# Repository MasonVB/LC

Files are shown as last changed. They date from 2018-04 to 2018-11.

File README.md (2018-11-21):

## DESIGN AND CONTROL OF A HIGH PRECISION LASER CUTTING MACHINE
  This repository includes all files files related to the reproduction of a high precision laser cutting machine. This machine is the topic of paper IMECE2018-88131 from the ASME 2018 International Mechanical Engineering Congress and Exposition, November 9-15, 2018, Pittsburgh, Pennsylvania, USA

  This repository is divided into three sections: the SolidWorks model, the .STL files used by 3D printers, and the drawings for each of the parts. 

  * To open the SolidWorks model: download the repository, navigate to the 3D Model Files - Solidworks folder, and open the LCOA-1.SLDASM file. For reference, all part numbers are described in the PN file located in the root folder.

  * To open the .STL files: download the repository and navigate to the 3D Printer Files folder.

  * To open the drawing files: download the repository, navigate to the Drawing Files folder, and then to the PDF folder. PDF versions of each drawing is located here.
  
### Please note:
This is an ongoing project. Therefore, although the 3D Printing files (.STL) should be up to date, the most up to date files will be the SolidWorks models. 

  Additionally, although there are drawing files for every part, only pertinent dimensions are given. As stated on every drawing, all dimensions are for reference and part fabrication shall be performed according to the solid models. If any discrepancies occur, the solid model shall be assumed to be correct.

  For more information or any questions, please contact me through the form located at the bottom of my website: www.MasonVB.com.

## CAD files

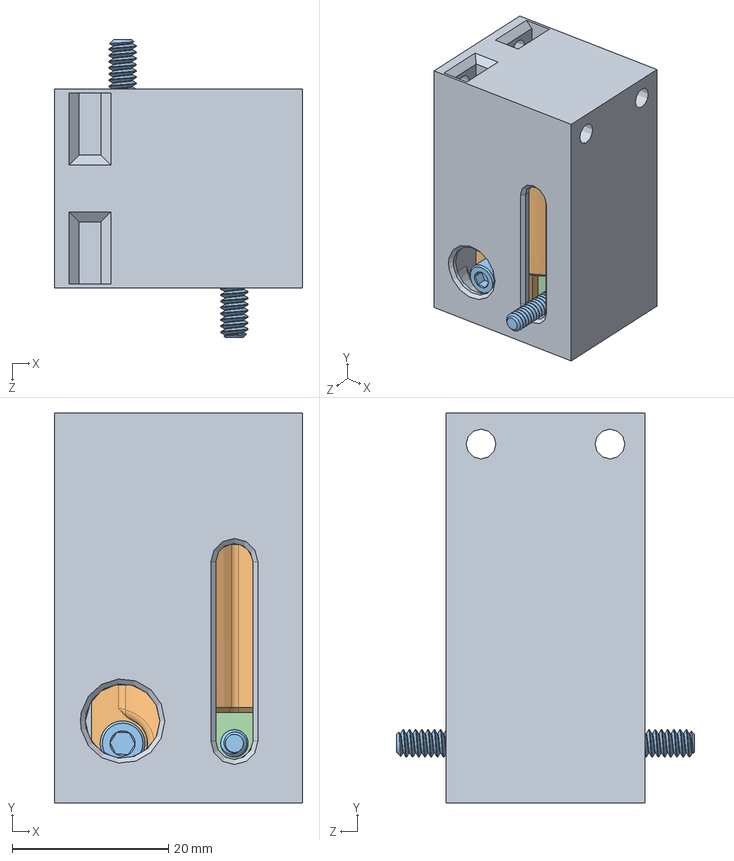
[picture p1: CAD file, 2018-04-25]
Pen Adapter/PEN ADAPTER.SLDASM
31.8 x 49.8 x 38.1 mm
PEN SLEEVE
PEN ADAPTER
92196A153 x 2
94855A201 x 2

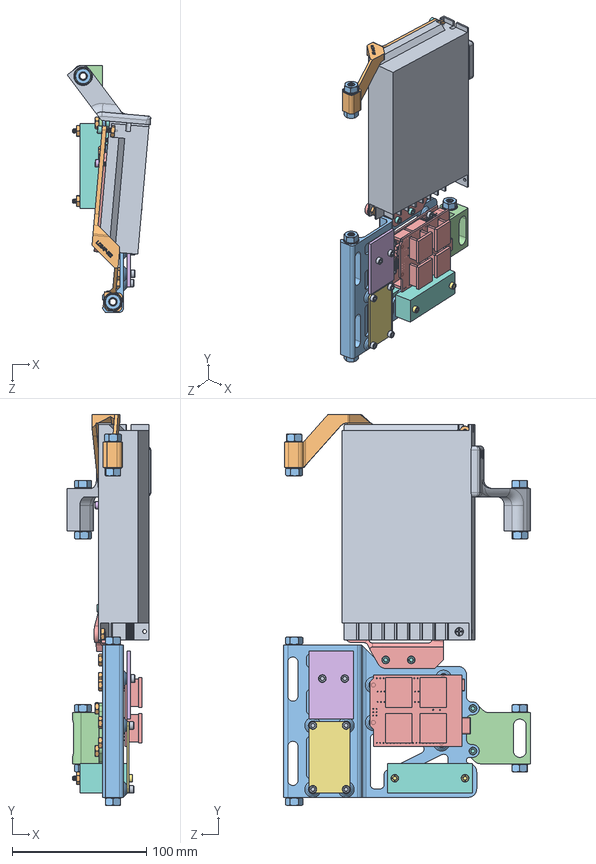
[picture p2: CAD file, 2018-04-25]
3D Model Files - Solidworks/LCSA-5.SLDASM
62.4 x 291.7 x 184.2 mm
LCSAP-501
LCSAP-502
LCSAP-503
LCSAP-504
LCSAP-505
91292A111 x 3
92196A237 x 2
92196A145 x 6
97334A146 x 10
90480A007 x 19
90473A029 x 8
91090A105 x 8
UNO-CNC
3.3V-5V
TB-1505L x 2
LRS-150-12
92210A145

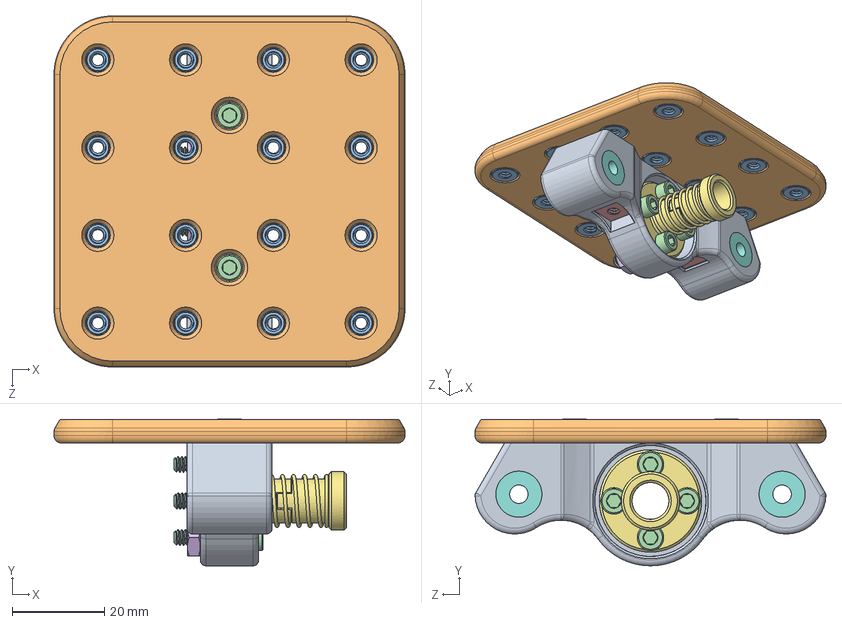
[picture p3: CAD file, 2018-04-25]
3D Model Files - Solidworks/LCSA-2.SLDASM
76.2 x 31.9 x 76.2 mm
LCSAP-202
LCSAP-201
95117A433 x 16
92196A150 x 6
94855A201 x 2
90480A007 x 4
T8-AB
6659K650 x 2

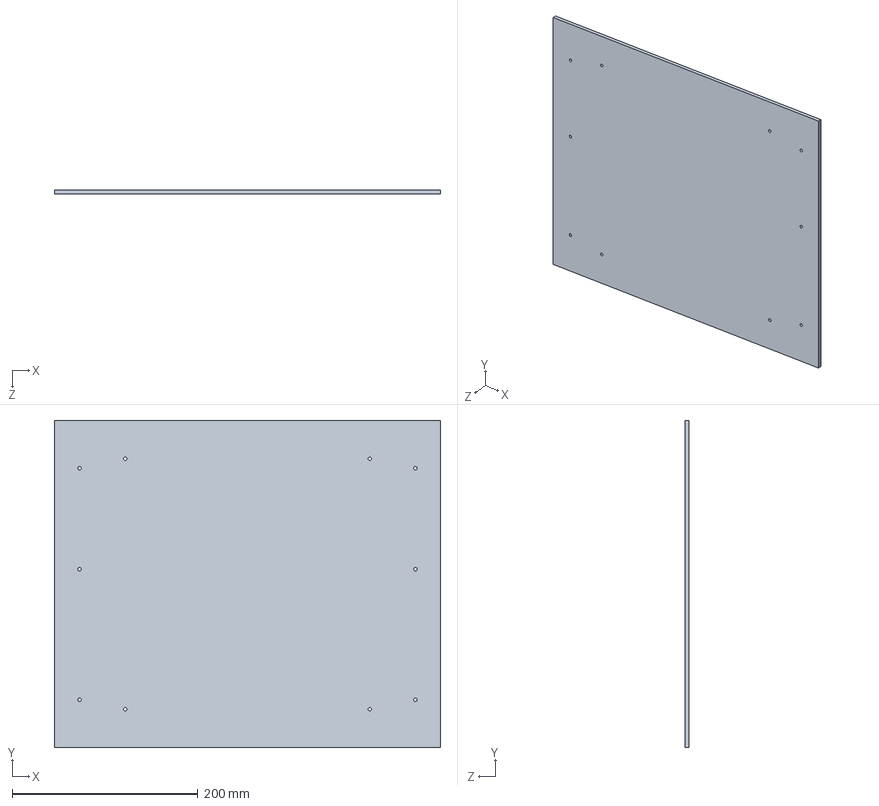
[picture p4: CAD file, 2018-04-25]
3D Model Files - Solidworks/LCSAP-607.SLDPRT
415.9 x 352.4 x 4.76 mm

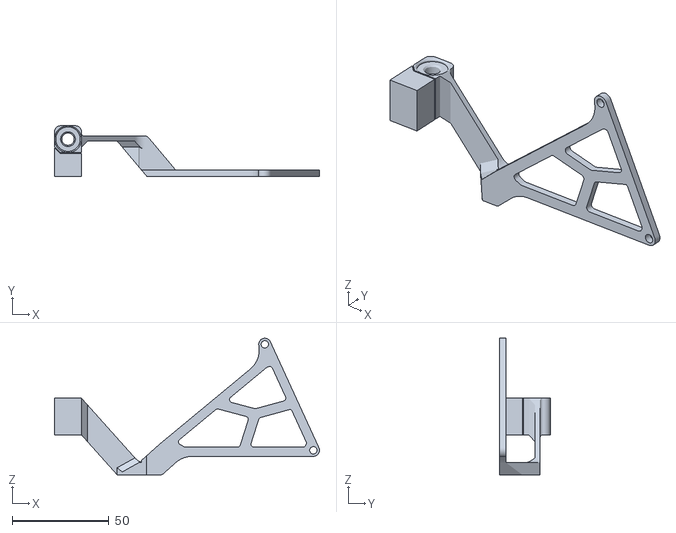
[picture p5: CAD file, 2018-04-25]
3D Printer Files/LCSAP-502.STL
137.2 x 26.2 x 70.7

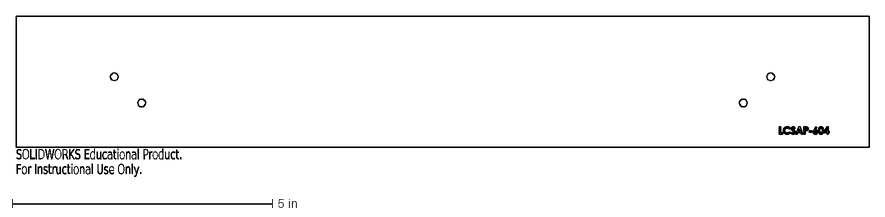
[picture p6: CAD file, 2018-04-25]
Laser Files/LCSAP-604.DXF
SOLIDWORKS Educational Product.
For Instructional Use Only.

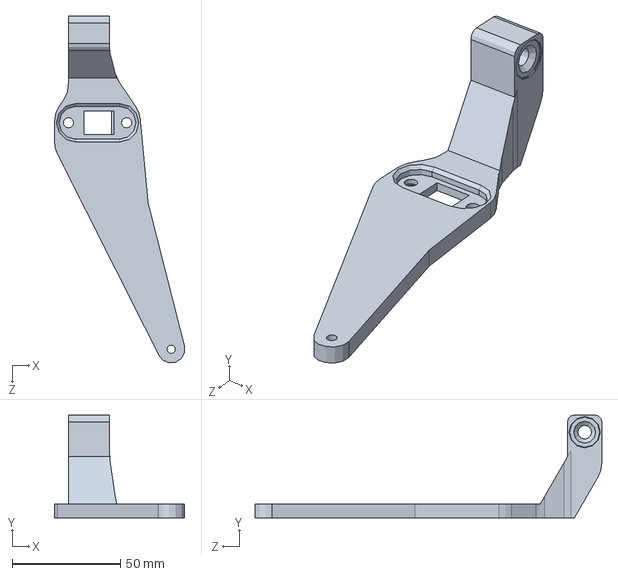
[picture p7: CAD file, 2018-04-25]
Skeleton Assembly/LCSKEL-2.SLDPRT
60.2 x 47.6 x 160.4 mm

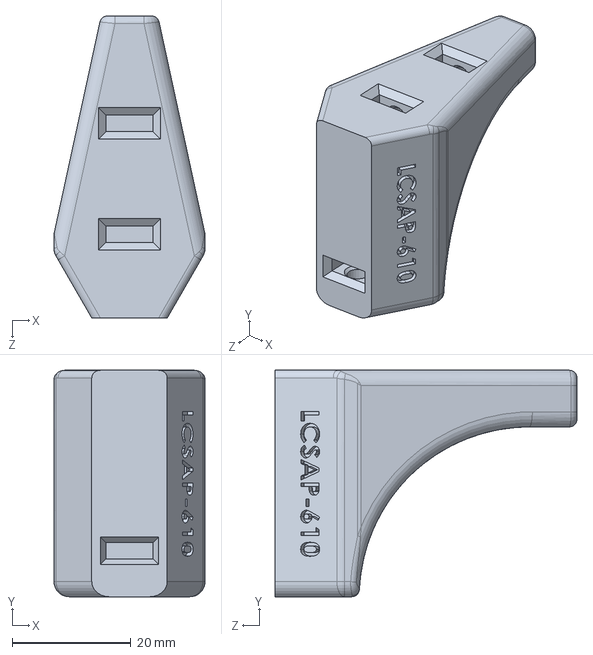
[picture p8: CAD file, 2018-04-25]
3D Model Files - Solidworks/LCSAP-610.SLDPRT
25.4 x 38.1 x 50.8 mm

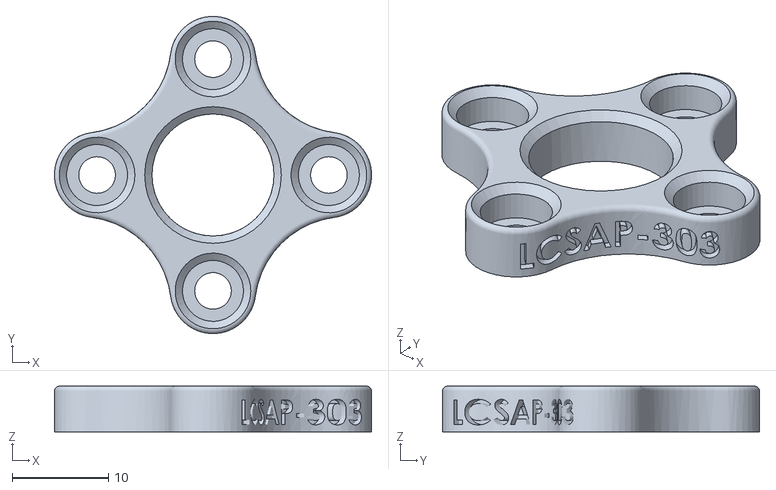
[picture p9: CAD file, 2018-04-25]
3D Printer Files/LCSAP-303.STL
33.0 x 33.0 x 4.76

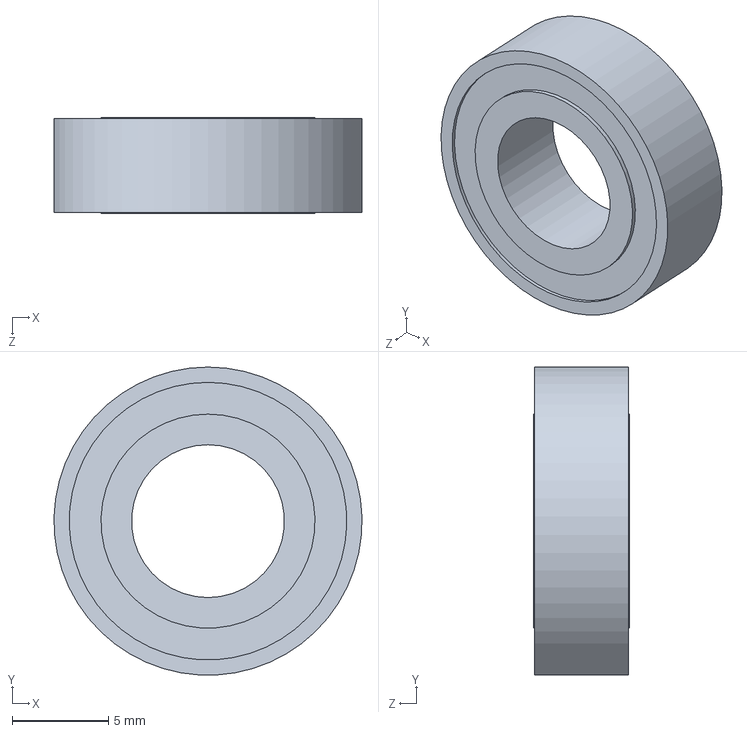
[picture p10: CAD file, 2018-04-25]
Hardware/R1810-2Z.SLDPRT
16.0 x 16.0 x 5.00 mm

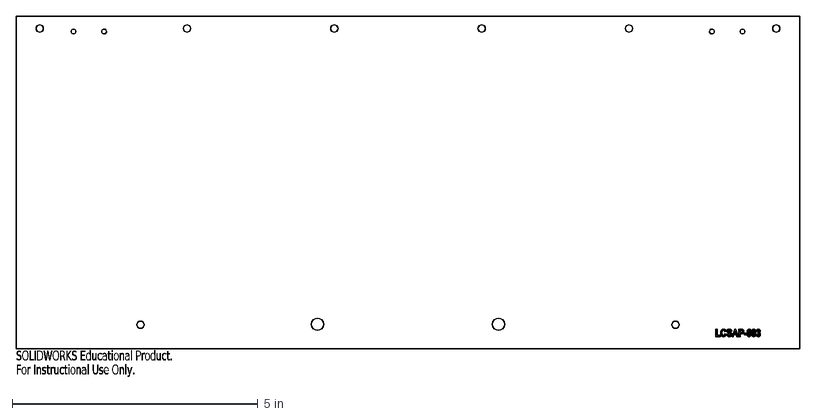
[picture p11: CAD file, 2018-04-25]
Laser Files/LCSAP-603.DXF
SOLIDWORKS Educational Product.
For Instructional Use Only.

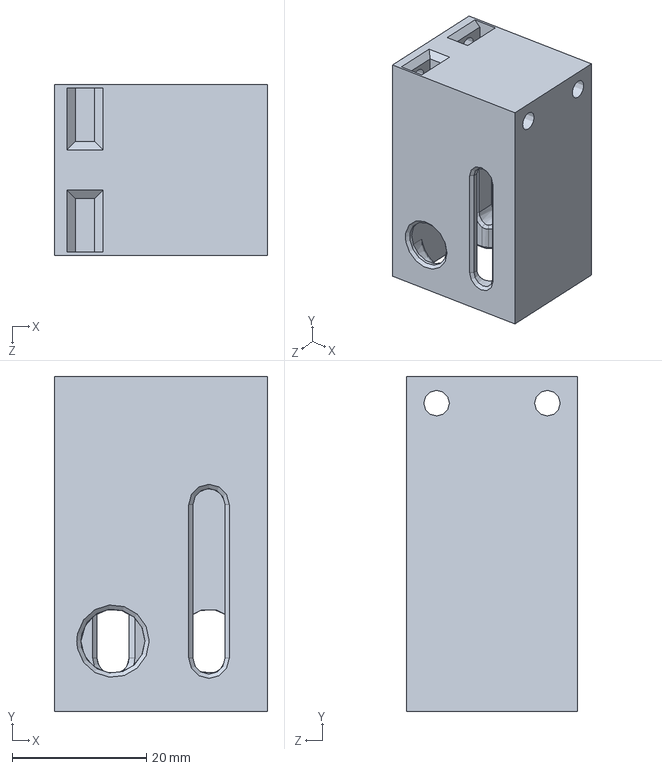
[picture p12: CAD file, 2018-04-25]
Pen Adapter/PEN SLEEVE.SLDPRT
31.8 x 49.8 x 25.4 mm

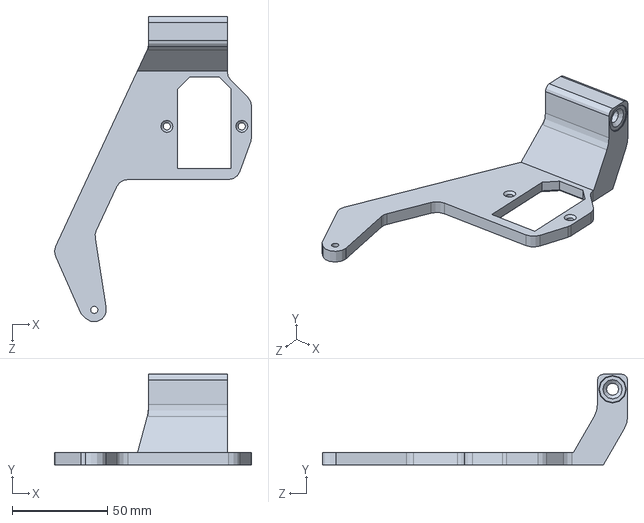
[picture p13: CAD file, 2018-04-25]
Skeleton Assembly/LCSKEL-1.SLDPRT
103.5 x 47.6 x 160.3 mm

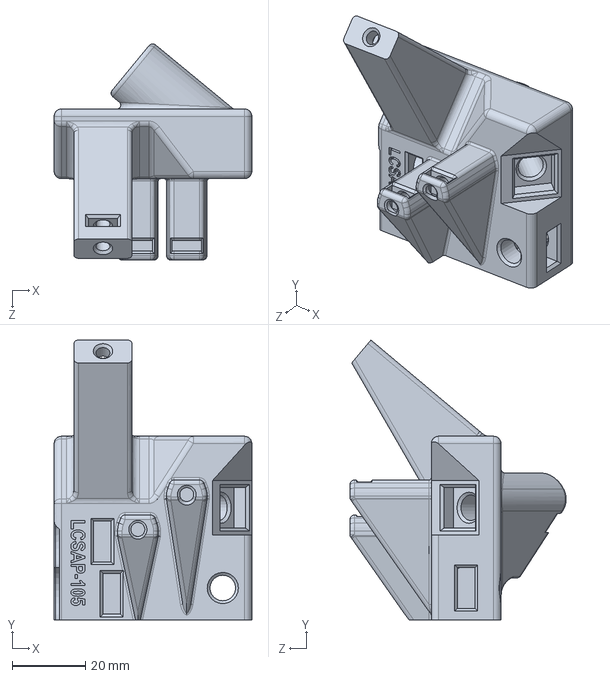
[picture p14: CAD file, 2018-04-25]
3D Model Files - Solidworks/LCSAP-105.SLDPRT
54.0 x 76.4 x 59.0 mm

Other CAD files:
3D Printer Files/LCSAP-104.STL
Laser Files/LCSAP-602.DXF
3D Printer Files/LCSAP-304.STL
Laser Files/LCSAP-606.DXF
3D Model Files - Solidworks/LCMP-101.SLDPRT
3D Model Files - Solidworks/LCSAP-101.SLDPRT
3D Model Files - Solidworks/LCSAP-102.SLDPRT
3D Model Files - Solidworks/LCSAP-103.SLDPRT
3D Model Files - Solidworks/LCSAP-104.SLDPRT
3D Model Files - Solidworks/LCSAP-106.SLDPRT
3D Model Files - Solidworks/LCSAP-107.SLDPRT
3D Model Files - Solidworks/LCSAP-201.SLDPRT
3D Model Files - Solidworks/LCSAP-202.SLDPRT
3D Model Files - Solidworks/LCSAP-301.SLDPRT
3D Model Files - Solidworks/LCSAP-302.SLDPRT
3D Model Files - Solidworks/LCSAP-303.SLDPRT
3D Model Files - Solidworks/LCSAP-304.SLDPRT
3D Model Files - Solidworks/LCSAP-403.SLDPRT
3D Model Files - Solidworks/LCSAP-501.SLDPRT
3D Model Files - Solidworks/LCSAP-502.SLDPRT
3D Model Files - Solidworks/LCSAP-503.SLDPRT
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

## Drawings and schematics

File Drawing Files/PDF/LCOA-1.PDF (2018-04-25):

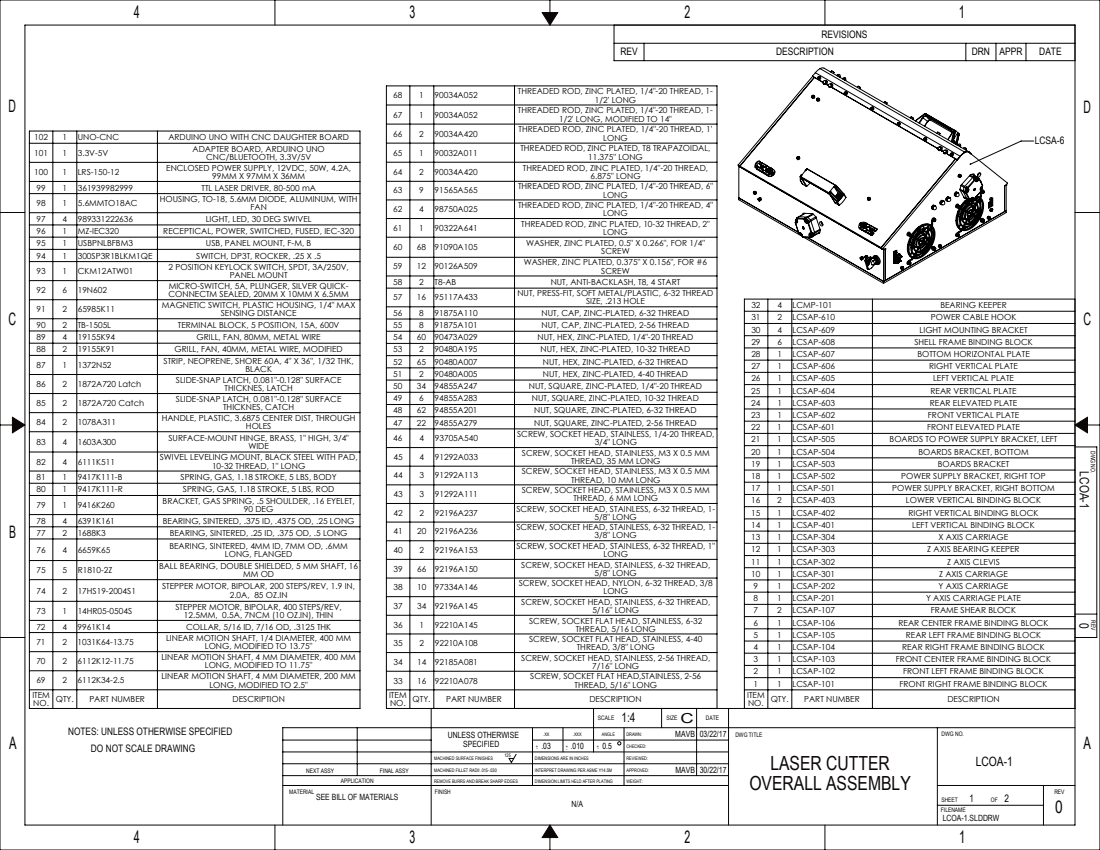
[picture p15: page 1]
QTY.; PART NUMBER; DESCRIPTION; ADAPTER BOARD, ARDUINO UNO; CNC/BLUETOOTH, 3.3V/5V; LRS-150-12; ENCLOSED POWER SUPPLY, 12VDC, 50W, 4.2A,; TTL LASER DRIVER, 80-500 mA; USBPNLBFBM3; USB, PANEL MOUNT, F-M, B; MAGNETIC SWITCH, PLASTIC HOUSING, 1/4" MAX; SENSING DISTANCE; TERMINAL BLOCK, 5 POSITION, 15A, 600V; GRILL, FAN, 80MM, METAL WIRE; GRILL, FAN, 40MM, METAL WIRE, MODIFIED; STRIP, NEOPRENE, SHORE 60A, 4" X 36", 1/32 THK,; 1872A720 Catch; SLIDE-SNAP LATCH, 0.081"-0.128" SURFACE; THICKNES, CATCH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

REVISIONS

REV | DESCRIPTION | DRN | APPR | DATE

68 | 1 | 90034A052 | THREADED ROD, ZINC PLATED, 1/4"-20 THREAD, 1-1/2' LONG
67 | 1 | 90034A052 | THREADED ROD, ZINC PLATED, 1/4"-20 THREAD, 1-1/2' LONG, MODIFIED TO 14"
66 | 2 | 90034A420 | THREADED ROD, ZINC PLATED, 1/4"-20 THREAD, 1' LONG

102 | 1 | UNO-CNC | ARDUINO UNO WITH CNC DAUGHTER BOARD

98 | 1 | 5.6MMTO18AC | HOUSING, TO-18, 5.6MM DIODE, ALUMINUM, WITH FAN
97 | 4 | 989331222636 | LIGHT, LED, 30 DEG SWIVEL
96 | 1 | MZ-IEC320 | RECEPTICAL, POWER, SWITCHED, FUSED, IEC-320

62 | 4 | 98750A025 | THREADED ROD, ZINC PLATED, 1/4"-20 THREAD, 4" LONG
61 | 1 | 90322A641 | THREADED ROD, ZINC PLATED, 10-32 THREAD, 2" LONG

94 | 1 | 300SP3R1BLKM1QE | SWITCH, DP3T, ROCKER, .25 X .5
93 | 1 | CKM12ATW01 | 2 POSITION KEYLOCK SWITCH, SPDT, 3A/250V, PANEL MOUNT
92 | 6 | 19N602 | MICRO-SWITCH, 5A, PLUNGER, SILVER QUICK-CONNECTM SEALED, 20MM X 10MM X 6.5MM

59 | 12 | 90126A509 | WASHER, ZINC PLATED, 0.375" X 0.156", FOR #6 SCREW
58 | 2 | T8-AB | NUT, ANTI-BACKLASH, T8, 4 START
57 | 16 | 95117A433 | NUT, PRESS-FIT, SOFT METAL/PLASTIC, 6-32 THREAD SIZE, .213 HOLE
56 | 8 | 91875A110 | NUT, CAP, ZINC-PLATED, 6-32 THREAD

31 | 2 | LCSAP-610 | POWER CABLE HOOK
30 | 4 | LCSAP-609 | LIGHT MOUNTING BRACKET
29 | 6 | LCSAP-608 | SHELL FRAME BINDING BLOCK
28 | 1 | LCSAP-607 | BOTTOM HORIZONTAL PLATE
27 | 1 | LCSAP-606 | RIGHT VERTICAL PLATE
26 | 1 | LCSAP-605 | LEFT VERTICAL PLATE
25 | 1 | LCSAP-604 | REAR VERTICAL PLATE
24 | 1 | LCSAP-603 | REAR ELEVATED PLATE
23 | 1 | LCSAP-602 | FRONT VERTICAL PLATE
22 | 1 | LCSAP-601 | FRONT ELEVATED PLATE

51 | 2 | 90480A005 | NUT, HEX, ZINC-PLATED, 4-40 THREAD
50 | 34 | 94855A247 | NUT, SQUARE, ZINC-PLATED, 1/4"-20 THREAD

86 | 2 | 1872A720 Latch | SLIDE-SNAP LATCH, 0.081"-0.128" SURFACE THICKNES, LATCH

48 | 62 | 94855A201 | NUT, SQUARE, ZINC-PLATED, 6-32 THREAD
47 | 22 | 94855A279 | NUT, SQUARE, ZINC-PLATED, 2-56 THREAD
46 | 4 | 93705A540 | SCREW, SOCKET HEAD, STAINLESS, 1/4-20 THREAD, 3/4" LONG
45 | 4 | 91292A033 | SCREW, SOCKET HEAD, STAINLESS, M3 X 0.5 MM THREAD, 35 MM LONG
44 | 3 | 91292A113 | SCREW, SOCKET HEAD, STAINLESS, M3 X 0.5 MM THREAD, 10 MM LONG

84 | 2 | 1078A311 | HANDLE, PLASTIC, 3.6875 CENTER DIST, THROUGH HOLES

20 | 1 | LCSAP-504 | BOARDS BRACKET, BOTTOM
19 | 1 | LCSAP-503 | BOARDS BRACKET

82 | 4 | 6111K511 | SWIVEL LEVELING MOUNT, BLACK STEEL WITH PAD, 10-32 THREAD, 1" LONG

REV DWG NO.

THREAD, 6 MM LONG

42 | 2 | 92196A237 | SCREW, SOCKET HEAD, STAINLESS, 6-32 THREAD, 1-5/8" LONG
41 | 20 | 92196A236 | SCREW, SOCKET HEAD, STAINLESS, 6-32 THREAD, 1-3/8" LONG
40 | 2 | 92196A153 | SCREW, SOCKET HEAD, STAINLESS, 6-32 THREAD, 1" LONG

15 | 1 | LCSAP-402 | RIGHT VERTICAL BINDING BLOCK
14 | 1 | LCSAP-401 | LEFT VERTICAL BINDING BLOCK
13 | 1 | LCSAP-304 | X AXIS CARRIAGE
12 | 1 | LCSAP-303 | Z AXIS BEARING KEEPER
11 | 1 | LCSAP-302 | Z AXIS CLEVIS
10 | 1 | LCSAP-301 | Z AXIS CARRIAGE

78 | 4 | 6391K161 | BEARING, SINTERED, .375 ID, .4375 OD, .25 LONG
77 | 2 | 1688K3 | BEARING, SINTERED, .25 ID, .375 OD, .5 LONG
76 | 4 | 6659K65 | BEARING, SINTERED, 4MM ID, 7MM OD, .6MM LONG, FLANGED

38 | 10 | 97334A146 | SCREW, SOCKET HEAD, NYLON, 6-32 THREAD, 3/8 LONG
37 | 34 | 92196A145 | SCREW, SOCKET HEAD, STAINLESS, 6-32 THREAD, 5/16" LONG

8 | 1 | LCSAP-201 | Y AXIS CARRIAGE PLATE
7 | 2 | LCSAP-107 | FRAME SHEAR BLOCK

73 | 1 | 14HR05-0504S | STEPPER MOTOR, BIPOLAR, 400 STEPS/REV, 12.5MM, 0.5A, 7NCM (10 OZ.IN), THIN
72 | 4 | 9961K14 | COLLAR, 5/16 ID, 7/16 OD, .3125 THK

5 | 1 | LCSAP-105 | REAR LEFT FRAME BINDING BLOCK
4 | 1 | LCSAP-104 | REAR RIGHT FRAME BINDING BLOCK

LONG, MODIFIED TO 13.75"
LONG, MODIFIED TO 11.75"
LONG, MODIFIED TO 2.5"

2 | 1 | LCSAP-102 | FRONT LEFT FRAME BINDING BLOCK
1 | 1 | LCSAP-101 | FRONT RIGHT FRAME BINDING BLOCK

NOTES: UNLESS OTHERWISE SPECIFIED
DO NOT SCALE DRAWING

MACHINED FILLET RADII .015-.030
FINISH

INTERPRET DRAWING PER ASME Y14.5M

APPLICATION
SEE BILL OF MATERIALS
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

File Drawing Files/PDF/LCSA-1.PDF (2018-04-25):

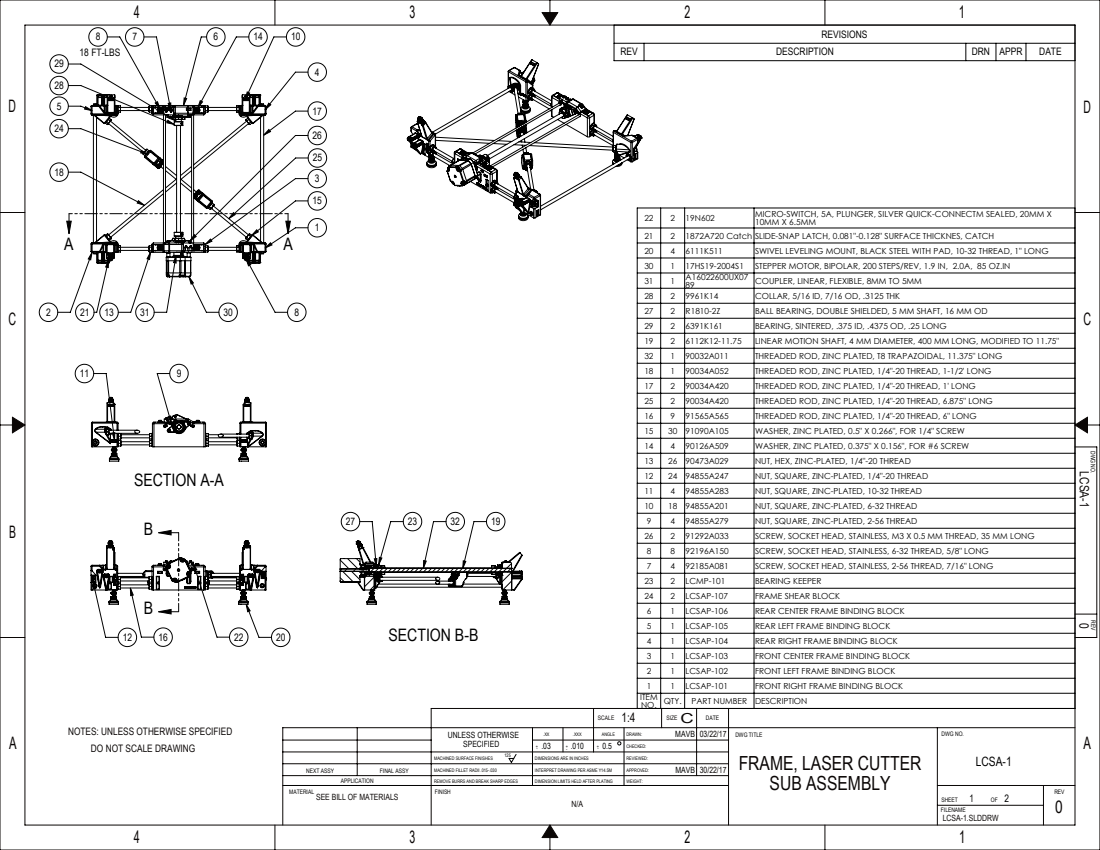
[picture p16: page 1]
SECTION A-A; SECTION B-B; 18 FT-LBS; NEXT ASSY; FINAL ASSY; REMOVE BURRS AND BREAK SHARP EDGES; DIMENSION LIMITS HELD AFTER PLATING; MACHINED SURFACE FINISHES; DIMENSIONS ARE IN INCHES 125; DWG TITLE; DWG NO.; UNLESS OTHERWISE; FRAME, LASER CUTTER SUB ASSEMBLY; 0 LCSA-1

REVISIONS

REV | DESCRIPTION | DRN | APPR | DATE

22 | 2 | 19N602 | MICRO-SWITCH, 5A, PLUNGER, SILVER QUICK-CONNECTM SEALED, 20MM X 10MM X 6.5MM
21 | 2 | 1872A720 Catch SLIDE-SNAP LATCH, 0.081"-0.128" SURFACE THICKNES, CATCH
20 | 4 | 6111K511 | SWIVEL LEVELING MOUNT, BLACK STEEL WITH PAD, 10-32 THREAD, 1" LONG
30 | 1 | 17HS19-2004S1 | STEPPER MOTOR, BIPOLAR, 200 STEPS/REV, 1.9 IN, 2.0A, 85 OZ.IN
31 | 1 | A16022600UX07 89 | COUPLER, LINEAR, FLEXIBLE, 8MM TO 5MM
28 | 2 | 9961K14 | COLLAR, 5/16 ID, 7/16 OD, .3125 THK
27 | 2 | R1810-2Z | BALL BEARING, DOUBLE SHIELDED, 5 MM SHAFT, 16 MM OD
29 | 2 | 6391K161 | BEARING, SINTERED, .375 ID, .4375 OD, .25 LONG
19 | 2 | 6112K12-11.75 | LINEAR MOTION SHAFT, 4 MM DIAMETER, 400 MM LONG, MODIFIED TO 11.75"
32 | 1 | 90032A011 | THREADED ROD, ZINC PLATED, T8 TRAPAZOIDAL, 11.375" LONG
18 | 1 | 90034A052 | THREADED ROD, ZINC PLATED, 1/4"-20 THREAD, 1-1/2' LONG
17 | 2 | 90034A420 | THREADED ROD, ZINC PLATED, 1/4"-20 THREAD, 1' LONG
25 | 2 | 90034A420 | THREADED ROD, ZINC PLATED, 1/4"-20 THREAD, 6.875" LONG
16 | 9 | 91565A565 | THREADED ROD, ZINC PLATED, 1/4"-20 THREAD, 6" LONG
15 | 30 | 91090A105 | WASHER, ZINC PLATED, 0.5" X 0.266", FOR 1/4" SCREW
14 | 4 | 90126A509 | WASHER, ZINC PLATED, 0.375" X 0.156", FOR #6 SCREW
13 | 26 | 90473A029 | NUT, HEX, ZINC-PLATED, 1/4"-20 THREAD
12 | 24 | 94855A247 | NUT, SQUARE, ZINC-PLATED, 1/4"-20 THREAD
11 | 4 | 94855A283 | NUT, SQUARE, ZINC-PLATED, 10-32 THREAD
10 | 18 | 94855A201 | NUT, SQUARE, ZINC-PLATED, 6-32 THREAD
9 | 4 | 94855A279 | NUT, SQUARE, ZINC-PLATED, 2-56 THREAD
26 | 2 | 91292A033 | SCREW, SOCKET HEAD, STAINLESS, M3 X 0.5 MM THREAD, 35 MM LONG
8 | 8 | 92196A150 | SCREW, SOCKET HEAD, STAINLESS, 6-32 THREAD, 5/8" LONG
7 | 4 | 92185A081 | SCREW, SOCKET HEAD, STAINLESS, 2-56 THREAD, 7/16" LONG
23 | 2 | LCMP-101 | BEARING KEEPER
24 | 2 | LCSAP-107 | FRAME SHEAR BLOCK
6 | 1 | LCSAP-106 | REAR CENTER FRAME BINDING BLOCK
5 | 1 | LCSAP-105 | REAR LEFT FRAME BINDING BLOCK
4 | 1 | LCSAP-104 | REAR RIGHT FRAME BINDING BLOCK
3 | 1 | LCSAP-103 | FRONT CENTER FRAME BINDING BLOCK
2 | 1 | LCSAP-102 | FRONT LEFT FRAME BINDING BLOCK
1 | 1 | LCSAP-101 | FRONT RIGHT FRAME BINDING BLOCK
ITEM NO. | QTY. | PART NUMBER | DESCRIPTION

REV DWG NO.

NOTES: UNLESS OTHERWISE SPECIFIED

DO NOT SCALE DRAWING

MACHINED FILLET RADII .015-.030
FINISH

INTERPRET DRAWING PER ASME Y14.5M

APPLICATION
SEE BILL OF MATERIALS

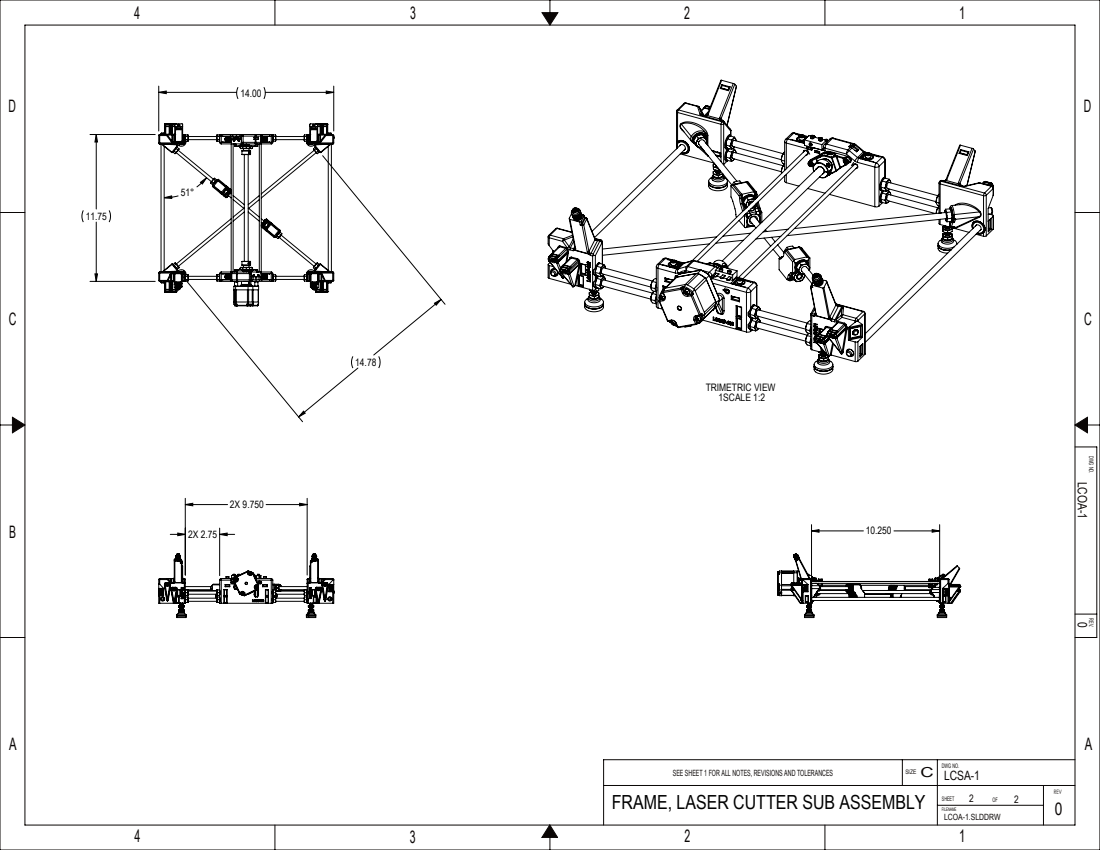
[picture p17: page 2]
TRIMETRIC VIEW 1SCALE 1:2; DWG NO.; 0 LCOA-1.SLDDRW; SIZE C

REV. DWG NO.

SEE SHEET 1 FOR ALL NOTES, REVISIONS AND TOLERANCES
FRAME, LASER CUTTER SUB ASSEMBLY

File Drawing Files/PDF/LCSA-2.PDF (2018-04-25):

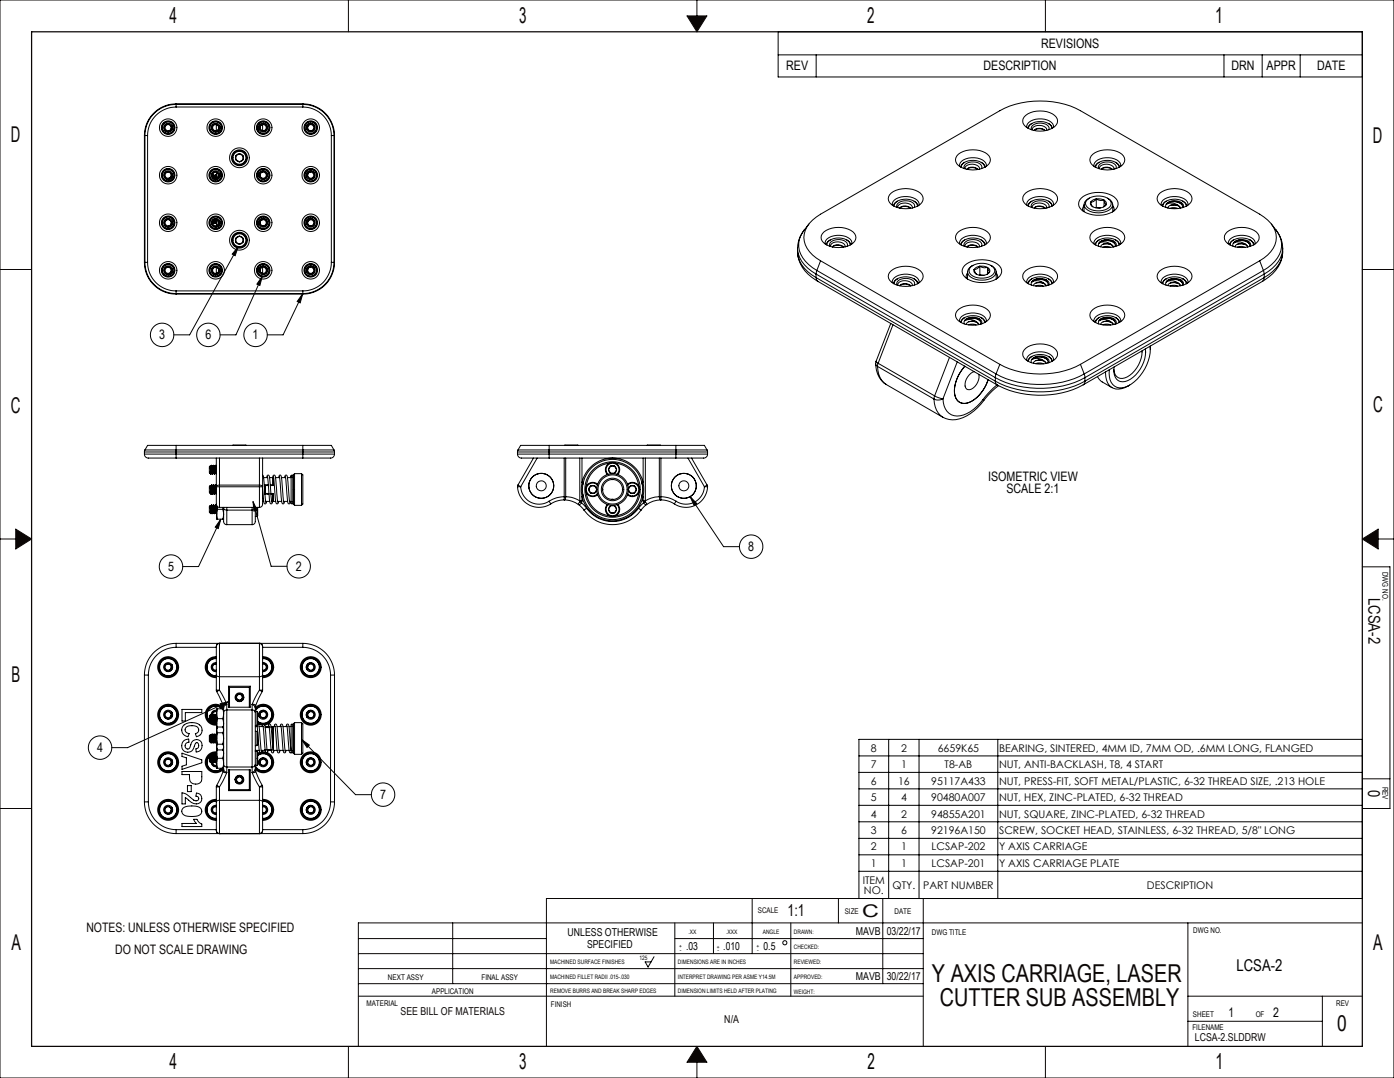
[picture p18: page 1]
ISOMETRIC VIEW SCALE 2:1; NEXT ASSY; FINAL ASSY; REMOVE BURRS AND BREAK SHARP EDGES; DIMENSION LIMITS HELD AFTER PLATING; MACHINED SURFACE FINISHES; DIMENSIONS ARE IN INCHES 125; DWG TITLE; DWG NO.; UNLESS OTHERWISE; Y AXIS CARRIAGE, LASER CUTTER SUB ASSEMBLY; 0 LCSA-2

REVISIONS

REV | DESCRIPTION | DRN | APPR | DATE

REV DWG NO.

8 | 2 | 6659K65 | BEARING, SINTERED, 4MM ID, 7MM OD, .6MM LONG, FLANGED
7 | 1 | T8-AB | NUT, ANTI-BACKLASH, T8, 4 START
6 | 16 | 95117A433 | NUT, PRESS-FIT, SOFT METAL/PLASTIC, 6-32 THREAD SIZE, .213 HOLE
5 | 4 | 90480A007 | NUT, HEX, ZINC-PLATED, 6-32 THREAD
4 | 2 | 94855A201 | NUT, SQUARE, ZINC-PLATED, 6-32 THREAD
3 | 6 | 92196A150 | SCREW, SOCKET HEAD, STAINLESS, 6-32 THREAD, 5/8" LONG
2 | 1 | LCSAP-202 | Y AXIS CARRIAGE
1 | 1 | LCSAP-201 | Y AXIS CARRIAGE PLATE
ITEM NO. | QTY. | PART NUMBER | DESCRIPTION

NOTES: UNLESS OTHERWISE SPECIFIED

DO NOT SCALE DRAWING

MACHINED FILLET RADII .015-.030
FINISH

INTERPRET DRAWING PER ASME Y14.5M

APPLICATION
SEE BILL OF MATERIALS

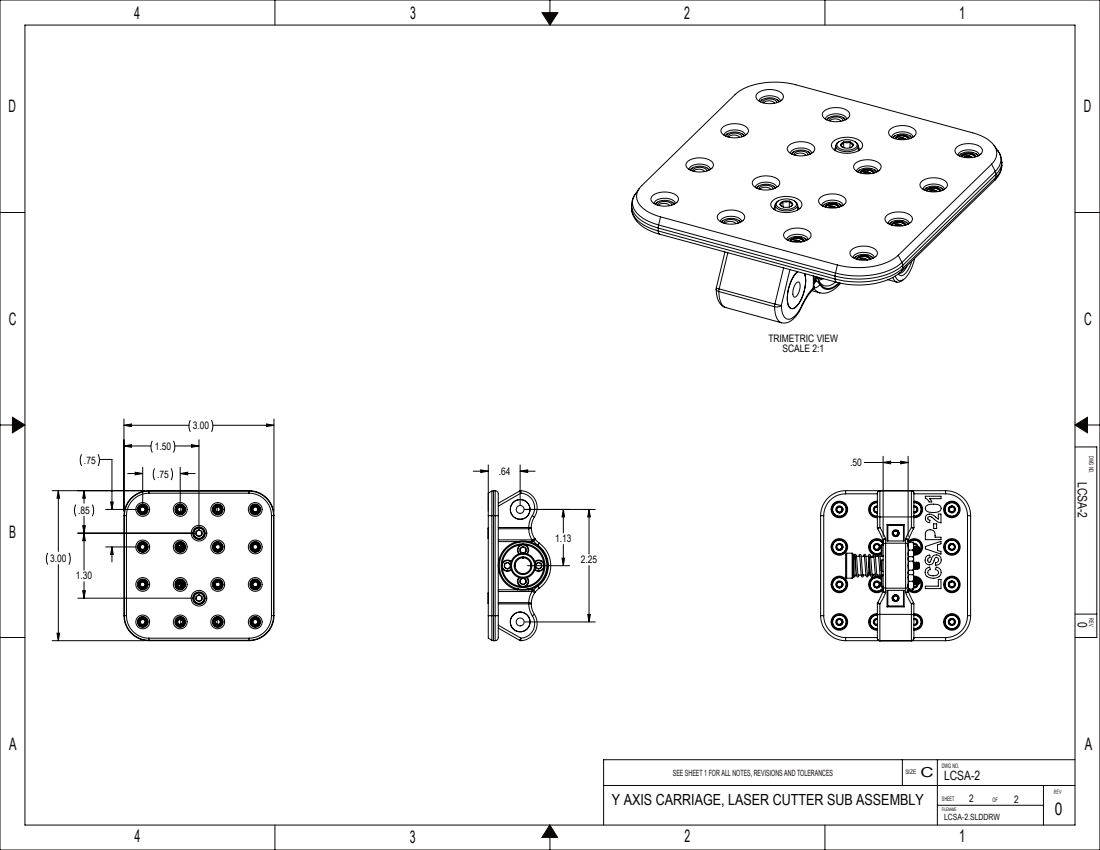
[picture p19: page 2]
TRIMETRIC VIEW SCALE 2:1; DWG NO.; 0 LCSA-2.SLDDRW; SIZE C

REV. DWG NO.

SEE SHEET 1 FOR ALL NOTES, REVISIONS AND TOLERANCES
Y AXIS CARRIAGE, LASER CUTTER SUB ASSEMBLY

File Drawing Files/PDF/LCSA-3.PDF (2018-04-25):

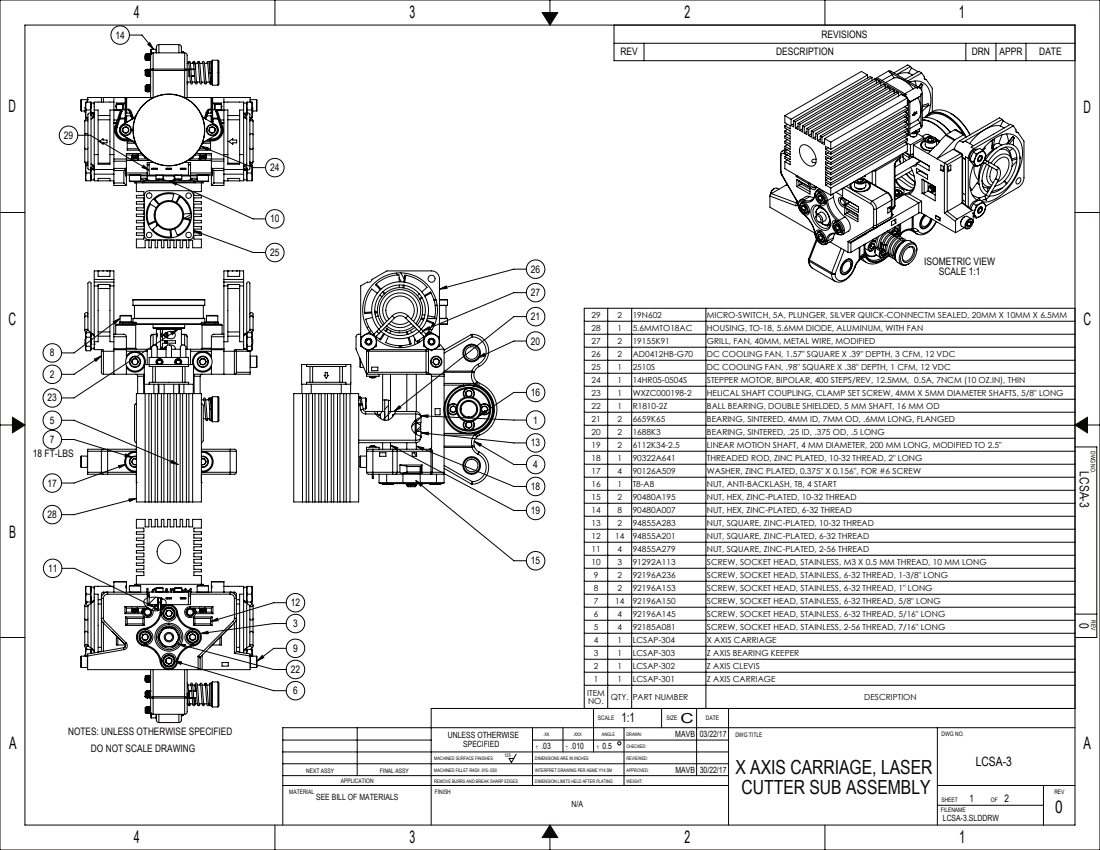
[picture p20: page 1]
18 FT-LBS; ISOMETRIC VIEW SCALE 1:1; NEXT ASSY; FINAL ASSY; REMOVE BURRS AND BREAK SHARP EDGES; DIMENSION LIMITS HELD AFTER PLATING; MACHINED SURFACE FINISHES; DIMENSIONS ARE IN INCHES 125; DWG TITLE; DWG NO.; UNLESS OTHERWISE; X AXIS CARRIAGE, LASER CUTTER SUB ASSEMBLY; 0 LCSA-3

REVISIONS

REV | DESCRIPTION | DRN | APPR | DATE

29 | 2 | 19N602 | MICRO-SWITCH, 5A, PLUNGER, SILVER QUICK-CONNECTM SEALED, 20MM X 10MM X 6.5MM
28 | 1 | 5.6MMTO18AC | HOUSING, TO-18, 5.6MM DIODE, ALUMINUM, WITH FAN
27 | 2 | 19155K91 | GRILL, FAN, 40MM, METAL WIRE, MODIFIED
26 | 2 | AD0412HB-G70 | DC COOLING FAN, 1.57" SQUARE X .39" DEPTH, 3 CFM, 12 VDC
25 | 1 | 2510S | DC COOLING FAN, .98" SQUARE X .38" DEPTH, 1 CFM, 12 VDC
24 | 1 | 14HR05-0504S | STEPPER MOTOR, BIPOLAR, 400 STEPS/REV, 12.5MM, 0.5A, 7NCM (10 OZ.IN), THIN
23 | 1 | WXZC000198-2 | HELICAL SHAFT COUPLING, CLAMP SET SCREW, 4MM X 5MM DIAMETER SHAFTS, 5/8" LONG
22 | 1 | R1810-2Z | BALL BEARING, DOUBLE SHIELDED, 5 MM SHAFT, 16 MM OD
21 | 2 | 6659K65 | BEARING, SINTERED, 4MM ID, 7MM OD, .6MM LONG, FLANGED
20 | 2 | 1688K3 | BEARING, SINTERED, .25 ID, .375 OD, .5 LONG
19 | 2 | 6112K34-2.5 | LINEAR MOTION SHAFT, 4 MM DIAMETER, 200 MM LONG, MODIFIED TO 2.5"
18 | 1 | 90322A641 | THREADED ROD, ZINC PLATED, 10-32 THREAD, 2" LONG
17 | 4 | 90126A509 | WASHER, ZINC PLATED, 0.375" X 0.156", FOR #6 SCREW
16 | 1 | T8-AB | NUT, ANTI-BACKLASH, T8, 4 START
15 | 2 | 90480A195 | NUT, HEX, ZINC-PLATED, 10-32 THREAD
14 | 8 | 90480A007 | NUT, HEX, ZINC-PLATED, 6-32 THREAD
13 | 2 | 94855A283 | NUT, SQUARE, ZINC-PLATED, 10-32 THREAD
12 | 14 | 94855A201 | NUT, SQUARE, ZINC-PLATED, 6-32 THREAD
11 | 4 | 94855A279 | NUT, SQUARE, ZINC-PLATED, 2-56 THREAD
10 | 3 | 91292A113 | SCREW, SOCKET HEAD, STAINLESS, M3 X 0.5 MM THREAD, 10 MM LONG
9 | 2 | 92196A236 | SCREW, SOCKET HEAD, STAINLESS, 6-32 THREAD, 1-3/8" LONG
8 | 2 | 92196A153 | SCREW, SOCKET HEAD, STAINLESS, 6-32 THREAD, 1" LONG
7 | 14 | 92196A150 | SCREW, SOCKET HEAD, STAINLESS, 6-32 THREAD, 5/8" LONG
6 | 4 | 92196A145 | SCREW, SOCKET HEAD, STAINLESS, 6-32 THREAD, 5/16" LONG
5 | 4 | 92185A081 | SCREW, SOCKET HEAD, STAINLESS, 2-56 THREAD, 7/16" LONG
4 | 1 | LCSAP-304 | X AXIS CARRIAGE
3 | 1 | LCSAP-303 | Z AXIS BEARING KEEPER
2 | 1 | LCSAP-302 | Z AXIS CLEVIS
1 | 1 | LCSAP-301 | Z AXIS CARRIAGE
ITEM NO. | QTY. | PART NUMBER | DESCRIPTION

REV DWG NO.

NOTES: UNLESS OTHERWISE SPECIFIED

DO NOT SCALE DRAWING

MACHINED FILLET RADII .015-.030
FINISH

INTERPRET DRAWING PER ASME Y14.5M

APPLICATION
SEE BILL OF MATERIALS

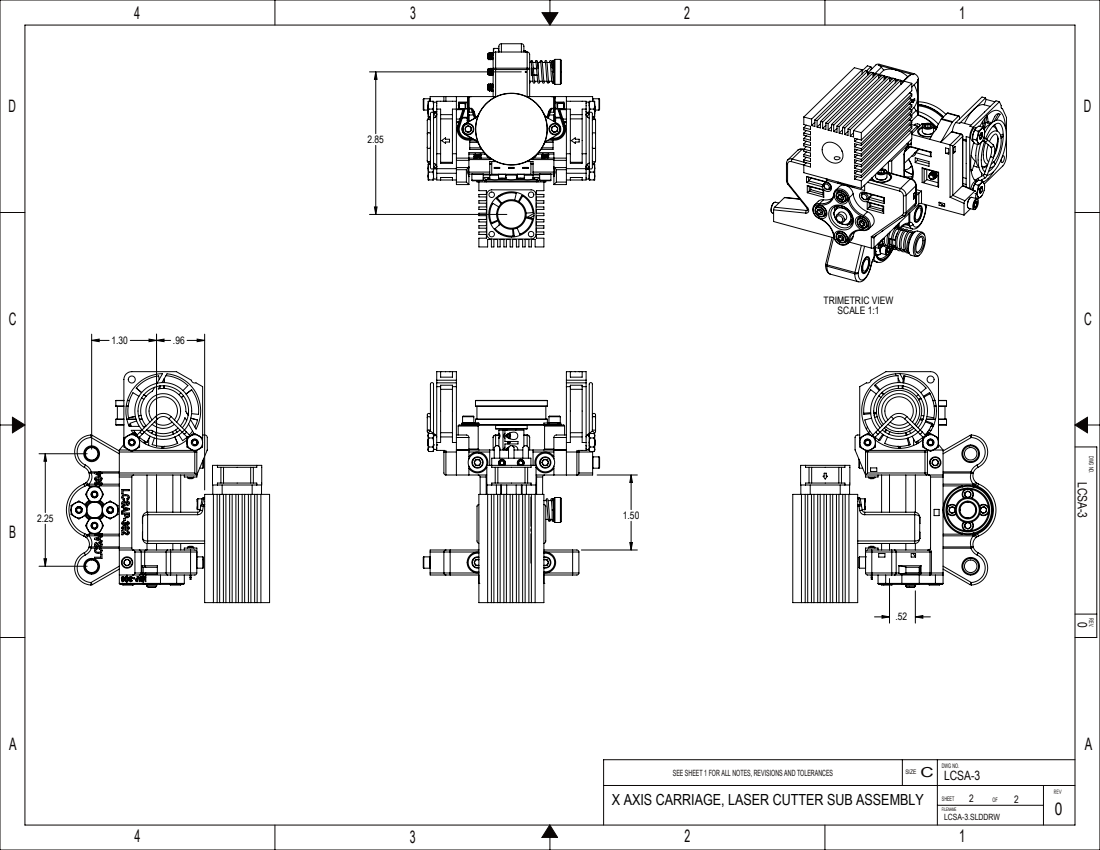
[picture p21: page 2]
TRIMETRIC VIEW SCALE 1:1; DWG NO.; 0 LCSA-3.SLDDRW; SIZE C

REV. DWG NO.

SEE SHEET 1 FOR ALL NOTES, REVISIONS AND TOLERANCES
X AXIS CARRIAGE, LASER CUTTER SUB ASSEMBLY

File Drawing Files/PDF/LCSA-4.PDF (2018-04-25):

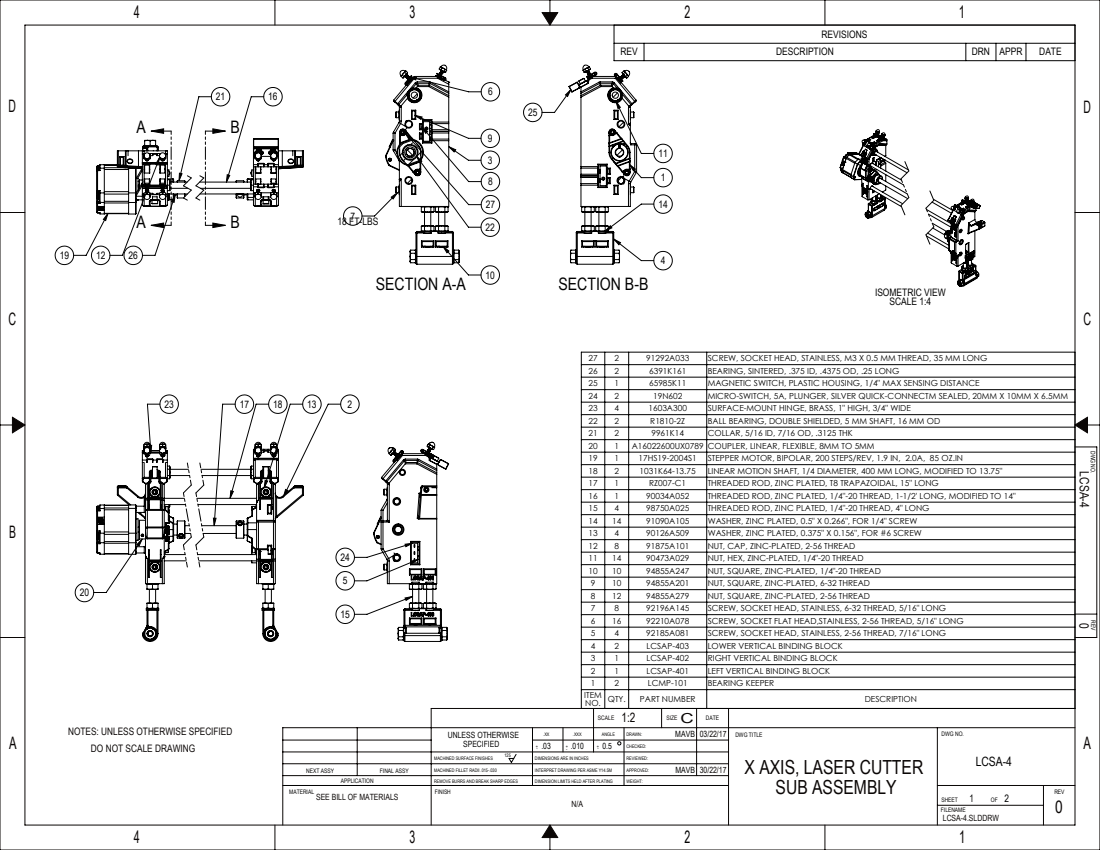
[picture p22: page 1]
SECTION A-A; SECTION B-B; ISOMETRIC VIEW SCALE 1:4; 18 FT-LBS; NEXT ASSY; FINAL ASSY; REMOVE BURRS AND BREAK SHARP EDGES; DIMENSION LIMITS HELD AFTER PLATING; MACHINED SURFACE FINISHES; DIMENSIONS ARE IN INCHES 125; DWG TITLE; DWG NO.; UNLESS OTHERWISE; X AXIS, LASER CUTTER SUB ASSEMBLY; 0 LCSA-4

REVISIONS

REV | DESCRIPTION | DRN | APPR | DATE

27 | 2 | 91292A033 | SCREW, SOCKET HEAD, STAINLESS, M3 X 0.5 MM THREAD, 35 MM LONG
26 | 2 | 6391K161 | BEARING, SINTERED, .375 ID, .4375 OD, .25 LONG
25 | 1 | 65985K11 | MAGNETIC SWITCH, PLASTIC HOUSING, 1/4" MAX SENSING DISTANCE
24 | 2 | 19N602 | MICRO-SWITCH, 5A, PLUNGER, SILVER QUICK-CONNECTM SEALED, 20MM X 10MM X 6.5MM
23 | 4 | 1603A300 | SURFACE-MOUNT HINGE, BRASS, 1" HIGH, 3/4" WIDE
22 | 2 | R1810-2Z | BALL BEARING, DOUBLE SHIELDED, 5 MM SHAFT, 16 MM OD
21 | 2 | 9961K14 | COLLAR, 5/16 ID, 7/16 OD, .3125 THK
20 | 1 | A16022600UX0789 | COUPLER, LINEAR, FLEXIBLE, 8MM TO 5MM
19 | 1 | 17HS19-2004S1 | STEPPER MOTOR, BIPOLAR, 200 STEPS/REV, 1.9 IN, 2.0A, 85 OZ.IN
18 | 2 | 1031K64-13.75 | LINEAR MOTION SHAFT, 1/4 DIAMETER, 400 MM LONG, MODIFIED TO 13.75"
17 | 1 | RZ007-C1 | THREADED ROD, ZINC PLATED, T8 TRAPAZOIDAL, 15" LONG
16 | 1 | 90034A052 | THREADED ROD, ZINC PLATED, 1/4"-20 THREAD, 1-1/2' LONG, MODIFIED TO 14"
15 | 4 | 98750A025 | THREADED ROD, ZINC PLATED, 1/4"-20 THREAD, 4" LONG
14 | 14 | 91090A105 | WASHER, ZINC PLATED, 0.5" X 0.266", FOR 1/4" SCREW
13 | 4 | 90126A509 | WASHER, ZINC PLATED, 0.375" X 0.156", FOR #6 SCREW
12 | 8 | 91875A101 | NUT, CAP, ZINC-PLATED, 2-56 THREAD
11 | 14 | 90473A029 | NUT, HEX, ZINC-PLATED, 1/4"-20 THREAD
10 | 10 | 94855A247 | NUT, SQUARE, ZINC-PLATED, 1/4"-20 THREAD
9 | 10 | 94855A201 | NUT, SQUARE, ZINC-PLATED, 6-32 THREAD
8 | 12 | 94855A279 | NUT, SQUARE, ZINC-PLATED, 2-56 THREAD
7 | 8 | 92196A145 | SCREW, SOCKET HEAD, STAINLESS, 6-32 THREAD, 5/16" LONG
6 | 16 | 92210A078 | SCREW, SOCKET FLAT HEAD,STAINLESS, 2-56 THREAD, 5/16" LONG
5 | 4 | 92185A081 | SCREW, SOCKET HEAD, STAINLESS, 2-56 THREAD, 7/16" LONG
4 | 2 | LCSAP-403 | LOWER VERTICAL BINDING BLOCK
3 | 1 | LCSAP-402 | RIGHT VERTICAL BINDING BLOCK
2 | 1 | LCSAP-401 | LEFT VERTICAL BINDING BLOCK
1 | 2 | LCMP-101 | BEARING KEEPER
ITEM NO. | QTY. | PART NUMBER | DESCRIPTION

REV DWG NO.

NOTES: UNLESS OTHERWISE SPECIFIED

DO NOT SCALE DRAWING

MACHINED FILLET RADII .015-.030
FINISH

INTERPRET DRAWING PER ASME Y14.5M

APPLICATION
SEE BILL OF MATERIALS

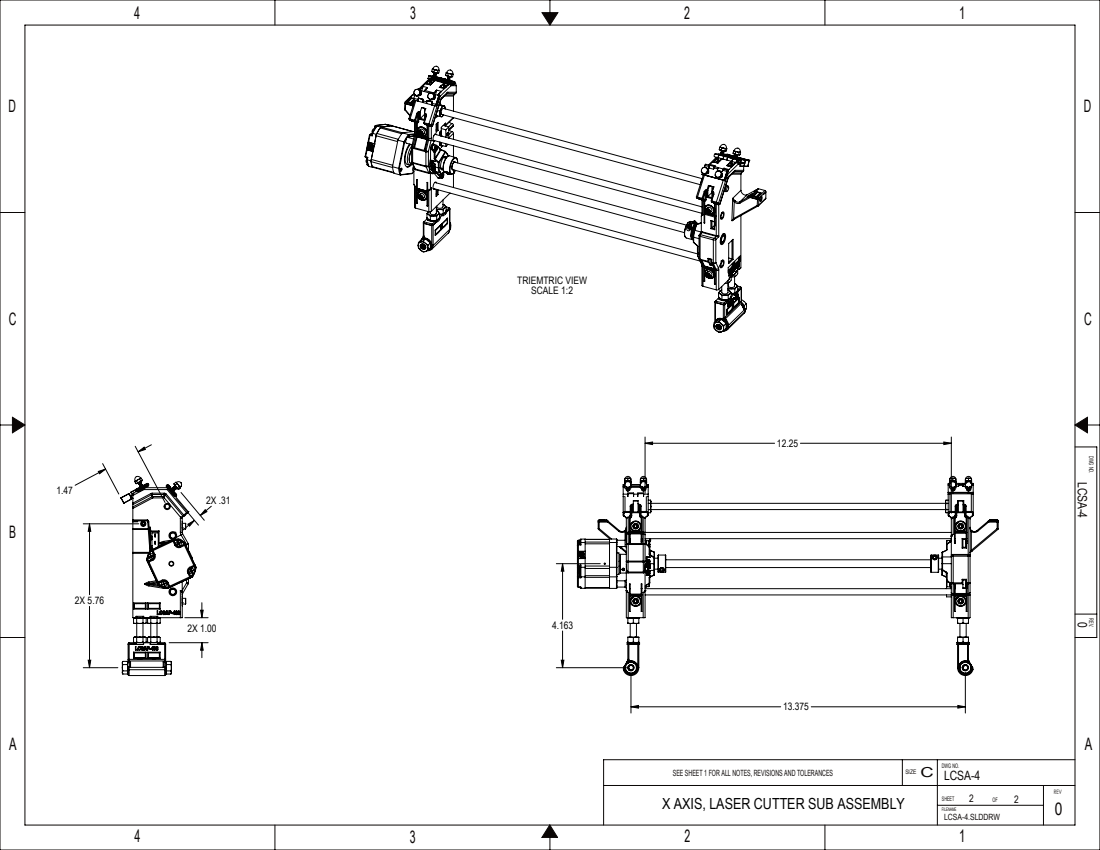
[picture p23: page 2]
TRIEMTRIC VIEW SCALE 1:2; DWG NO.; 0 LCSA-4.SLDDRW; SIZE C

REV. DWG NO.

SEE SHEET 1 FOR ALL NOTES, REVISIONS AND TOLERANCES
X AXIS, LASER CUTTER SUB ASSEMBLY

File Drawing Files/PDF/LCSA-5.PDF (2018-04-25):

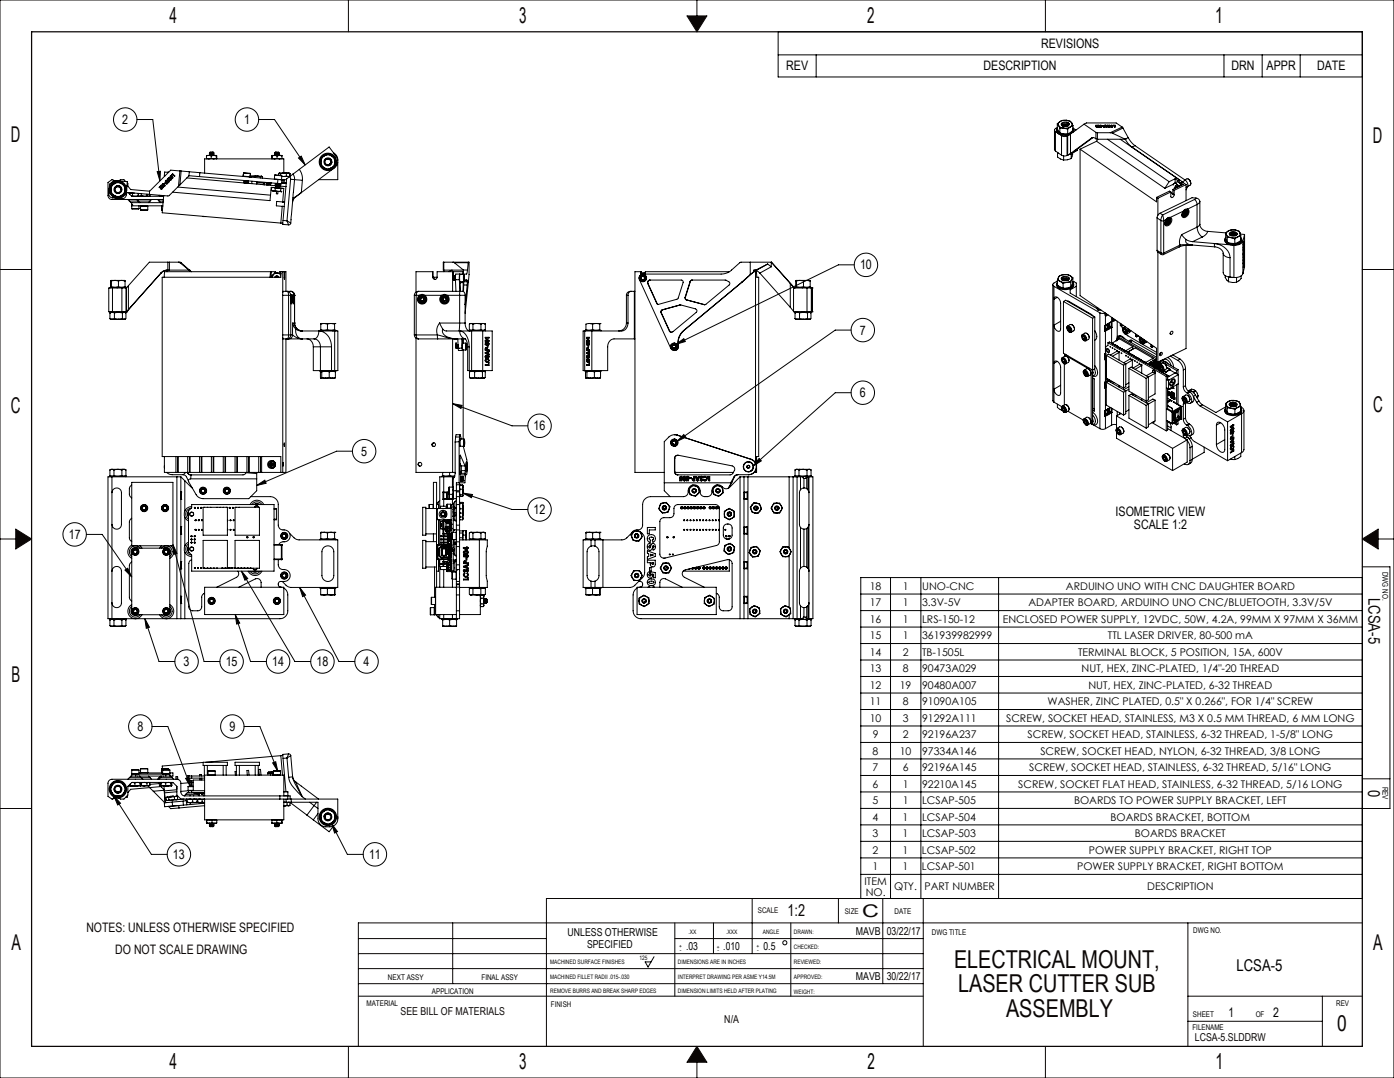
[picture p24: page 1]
ISOMETRIC VIEW SCALE 1:2; NEXT ASSY; FINAL ASSY; REMOVE BURRS AND BREAK SHARP EDGES; DIMENSION LIMITS HELD AFTER PLATING; MACHINED SURFACE FINISHES; DIMENSIONS ARE IN INCHES 125; DWG TITLE; DWG NO.; UNLESS OTHERWISE; ELECTRICAL MOUNT,; LASER CUTTER SUB; 0 LCSA-5

REVISIONS

REV | DESCRIPTION | DRN | APPR | DATE

REV DWG NO.

18 | 1 | UNO-CNC | ARDUINO UNO WITH CNC DAUGHTER BOARD
17 | 1 | 3.3V-5V | ADAPTER BOARD, ARDUINO UNO CNC/BLUETOOTH, 3.3V/5V
16 | 1 | LRS-150-12 | ENCLOSED POWER SUPPLY, 12VDC, 50W, 4.2A, 99MM X 97MM X 36MM
15 | 1 | 361939982999 | TTL LASER DRIVER, 80-500 mA
14 | 2 | TB-1505L | TERMINAL BLOCK, 5 POSITION, 15A, 600V
13 | 8 | 90473A029 | NUT, HEX, ZINC-PLATED, 1/4"-20 THREAD
12 | 19 | 90480A007 | NUT, HEX, ZINC-PLATED, 6-32 THREAD
11 | 8 | 91090A105 | WASHER, ZINC PLATED, 0.5" X 0.266", FOR 1/4" SCREW
10 | 3 | 91292A111 | SCREW, SOCKET HEAD, STAINLESS, M3 X 0.5 MM THREAD, 6 MM LONG
9 | 2 | 92196A237 | SCREW, SOCKET HEAD, STAINLESS, 6-32 THREAD, 1-5/8" LONG
8 | 10 | 97334A146 | SCREW, SOCKET HEAD, NYLON, 6-32 THREAD, 3/8 LONG
7 | 6 | 92196A145 | SCREW, SOCKET HEAD, STAINLESS, 6-32 THREAD, 5/16" LONG
6 | 1 | 92210A145 | SCREW, SOCKET FLAT HEAD, STAINLESS, 6-32 THREAD, 5/16 LONG
5 | 1 | LCSAP-505 | BOARDS TO POWER SUPPLY BRACKET, LEFT
4 | 1 | LCSAP-504 | BOARDS BRACKET, BOTTOM
3 | 1 | LCSAP-503 | BOARDS BRACKET
2 | 1 | LCSAP-502 | POWER SUPPLY BRACKET, RIGHT TOP
1 | 1 | LCSAP-501 | POWER SUPPLY BRACKET, RIGHT BOTTOM
ITEM NO. | QTY. | PART NUMBER | DESCRIPTION

NOTES: UNLESS OTHERWISE SPECIFIED

DO NOT SCALE DRAWING

MACHINED FILLET RADII .015-.030
FINISH

INTERPRET DRAWING PER ASME Y14.5M

APPLICATION
SEE BILL OF MATERIALS

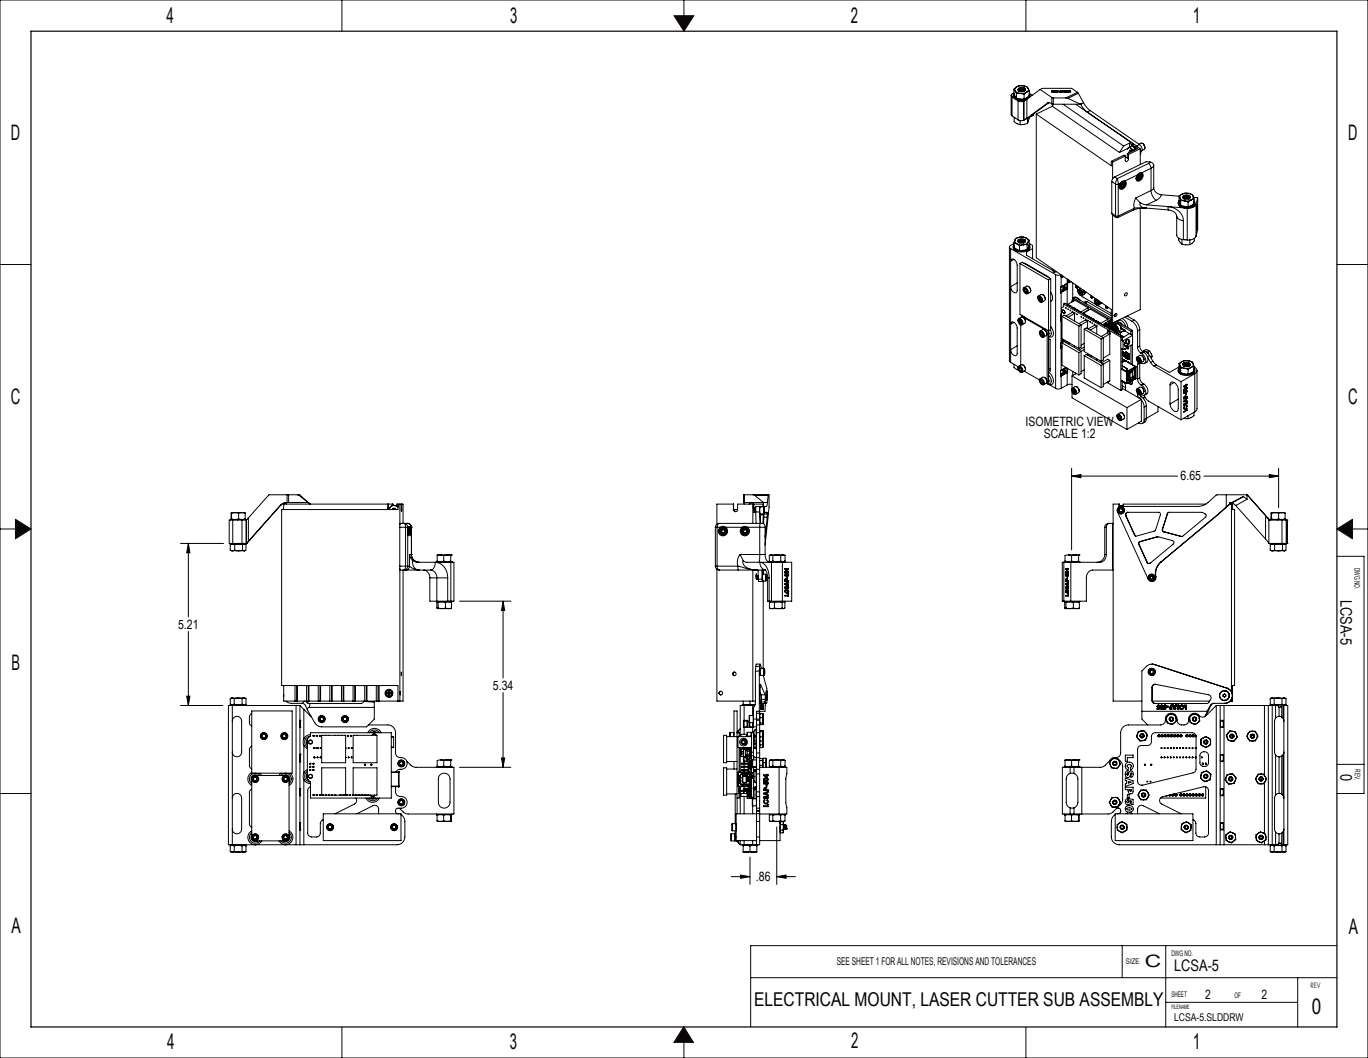
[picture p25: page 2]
ISOMETRIC VIEW SCALE 1:2; DWG NO.; 0 LCSA-5.SLDDRW; SIZE C

REV. DWG NO.

SEE SHEET 1 FOR ALL NOTES, REVISIONS AND TOLERANCES

ELECTRICAL MOUNT, LASER CUTTER SUB ASSEMBLY

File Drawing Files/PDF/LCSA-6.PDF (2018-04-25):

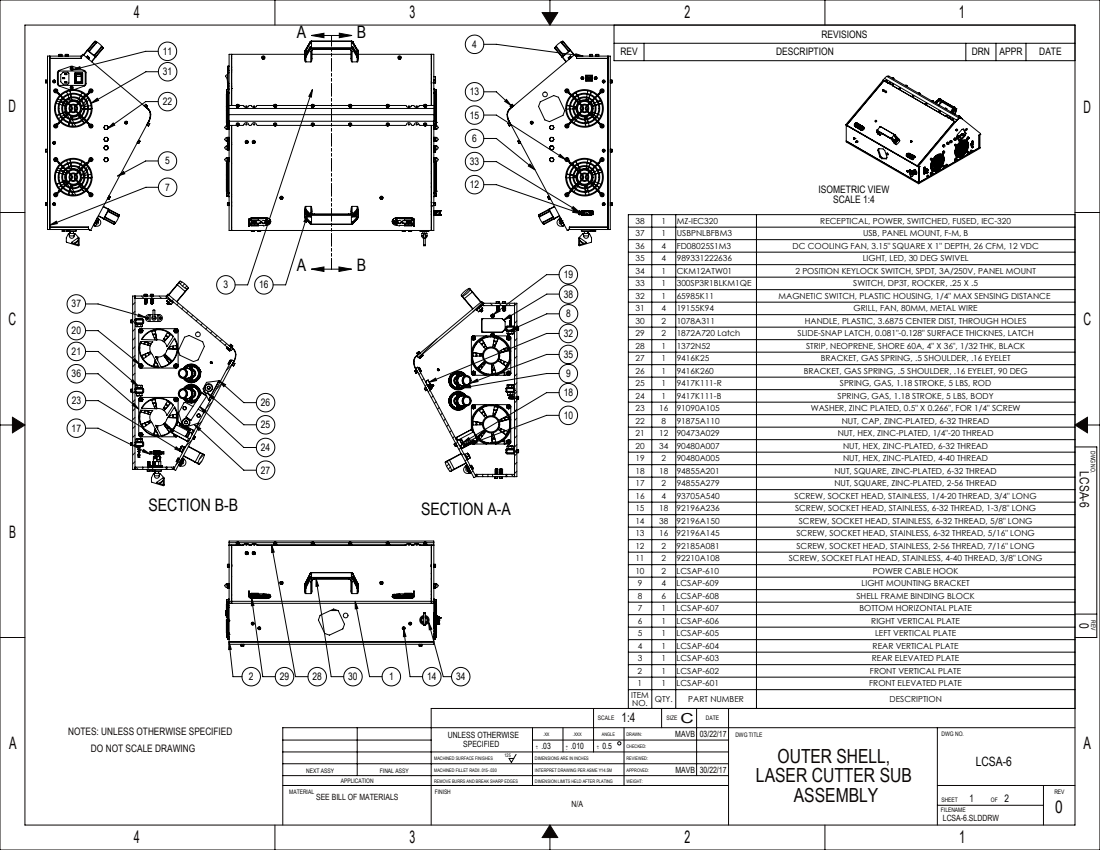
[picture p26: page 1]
SECTION A-A; SECTION B-B; ISOMETRIC VIEW SCALE 1:4; NEXT ASSY; FINAL ASSY; REMOVE BURRS AND BREAK SHARP EDGES; DIMENSION LIMITS HELD AFTER PLATING; MACHINED SURFACE FINISHES; DIMENSIONS ARE IN INCHES 125; DWG TITLE; DWG NO.; UNLESS OTHERWISE; OUTER SHELL,; LASER CUTTER SUB; 0 LCSA-6

REVISIONS

REV | DESCRIPTION | DRN | APPR | DATE

38 | 1 | MZ-IEC320 | RECEPTICAL, POWER, SWITCHED, FUSED, IEC-320
37 | 1 | USBPNLBFBM3 | USB, PANEL MOUNT, F-M, B
36 | 4 | FD08025S1M3 | DC COOLING FAN, 3.15" SQUARE X 1" DEPTH, 26 CFM, 12 VDC
35 | 4 | 989331222636 | LIGHT, LED, 30 DEG SWIVEL
34 | 1 | CKM12ATW01 | 2 POSITION KEYLOCK SWITCH, SPDT, 3A/250V, PANEL MOUNT
33 | 1 | 300SP3R1BLKM1QE | SWITCH, DP3T, ROCKER, .25 X .5
32 | 1 | 65985K11 | MAGNETIC SWITCH, PLASTIC HOUSING, 1/4" MAX SENSING DISTANCE
31 | 4 | 19155K94 | GRILL, FAN, 80MM, METAL WIRE
30 | 2 | 1078A311 | HANDLE, PLASTIC, 3.6875 CENTER DIST, THROUGH HOLES
29 | 2 | 1872A720 Latch | SLIDE-SNAP LATCH, 0.081"-0.128" SURFACE THICKNES, LATCH
28 | 1 | 1372N52 | STRIP, NEOPRENE, SHORE 60A, 4" X 36", 1/32 THK, BLACK
27 | 1 | 9416K25 | BRACKET, GAS SPRING, .5 SHOULDER, .16 EYELET
26 | 1 | 9416K260 | BRACKET, GAS SPRING, .5 SHOULDER, .16 EYELET, 90 DEG
25 | 1 | 9417K111-R | SPRING, GAS, 1.18 STROKE, 5 LBS, ROD
24 | 1 | 9417K111-B | SPRING, GAS, 1.18 STROKE, 5 LBS, BODY
23 | 16 | 91090A105 | WASHER, ZINC PLATED, 0.5" X 0.266", FOR 1/4" SCREW
22 | 8 | 91875A110 | NUT, CAP, ZINC-PLATED, 6-32 THREAD
21 | 12 | 90473A029 | NUT, HEX, ZINC-PLATED, 1/4"-20 THREAD
20 | 34 | 90480A007 | NUT, HEX, ZINC-PLATED, 6-32 THREAD
19 | 2 | 90480A005 | NUT, HEX, ZINC-PLATED, 4-40 THREAD
18 | 18 | 94855A201 | NUT, SQUARE, ZINC-PLATED, 6-32 THREAD
17 | 2 | 94855A279 | NUT, SQUARE, ZINC-PLATED, 2-56 THREAD
16 | 4 | 93705A540 | SCREW, SOCKET HEAD, STAINLESS, 1/4-20 THREAD, 3/4" LONG
15 | 18 | 92196A236 | SCREW, SOCKET HEAD, STAINLESS, 6-32 THREAD, 1-3/8" LONG
14 | 38 | 92196A150 | SCREW, SOCKET HEAD, STAINLESS, 6-32 THREAD, 5/8" LONG
13 | 16 | 92196A145 | SCREW, SOCKET HEAD, STAINLESS, 6-32 THREAD, 5/16" LONG
12 | 2 | 92185A081 | SCREW, SOCKET HEAD, STAINLESS, 2-56 THREAD, 7/16" LONG
11 | 2 | 92210A108 | SCREW, SOCKET FLAT HEAD, STAINLESS, 4-40 THREAD, 3/8" LONG
10 | 2 | LCSAP-610 | POWER CABLE HOOK
9 | 4 | LCSAP-609 | LIGHT MOUNTING BRACKET
8 | 6 | LCSAP-608 | SHELL FRAME BINDING BLOCK
7 | 1 | LCSAP-607 | BOTTOM HORIZONTAL PLATE
6 | 1 | LCSAP-606 | RIGHT VERTICAL PLATE
5 | 1 | LCSAP-605 | LEFT VERTICAL PLATE
4 | 1 | LCSAP-604 | REAR VERTICAL PLATE
3 | 1 | LCSAP-603 | REAR ELEVATED PLATE
2 | 1 | LCSAP-602 | FRONT VERTICAL PLATE
1 | 1 | LCSAP-601 | FRONT ELEVATED PLATE
ITEM NO. | QTY. | PART NUMBER | DESCRIPTION

REV DWG NO.

NOTES: UNLESS OTHERWISE SPECIFIED

DO NOT SCALE DRAWING

MACHINED FILLET RADII .015-.030
FINISH

INTERPRET DRAWING PER ASME Y14.5M

APPLICATION
SEE BILL OF MATERIALS

DETAIL VIEWS SCALE 1:2; TRIMETRIC VIEW SCALE 1:4; DWG NO.; 0 LCSA-6.SLDDRW; SIZE C

REV. DWG NO.

SEE SHEET 1 FOR ALL NOTES, REVISIONS AND TOLERANCES

OUTER SHELL ASSEMBLY, LASER CUTTER SUB ASSEMBLY

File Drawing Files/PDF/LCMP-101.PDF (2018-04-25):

SECTION A-A; ISOMETRIC VIEW SCALE 2:1; NEXT ASSY; FINAL ASSY; REMOVE BURRS AND BREAK SHARP EDGES; DIMENSION LIMITS HELD AFTER PLATING; MACHINED SURFACE FINISHES; DIMENSIONS ARE IN INCHES 125; DWG TITLE; DWG NO.; UNLESS OTHERWISE; POLYLACTIDE THERMOPLASTIC; BEARING KEEPER; 0 LCMP-103

REVISIONS

REV | DESCRIPTION | DRN | APPR | DATE

REV DWG NO.

DIMENSIONS GIVEN ARE STRICTLY FOR REFERENCE
ONLY. PART SHALL BE FABRICATED ACCORDING TO
SOLID MODEL. ALL DIMENSIONS SHALL BE TAKEN
OFF OF SOLID MODEL. IF DISCREPENCIES OCCURE,
SOLID MODEL SHALL BE ASSUMED TO BE CORRECT.

NOTES: UNLESS OTHERWISE SPECIFIED
DO NOT SCALE DRAWING

MACHINED FILLET RADII .015-.030
FINISH

INTERPRET DRAWING PER ASME Y14.5M

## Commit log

2018-04-25 Add files via upload
    First batch of files uploaded - Revision 0
    [LCMP-101.SLDDRW, LCMP-101.STL, LCOA-1.SLDDRW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]
2018-04-25 Add files via upload
    Second batch of files uploaded - Revision 0
    [LCMP-101.SLDPRT, LCSA-2.SLDASM, LCSA-5.SLDASM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]
2018-04-25 Add files via upload
    Third batch of files uploaded - Revision 0
    [1031K64-13.75.SLDPRT, 1078A311.SLDPRT, 1372N52.SLDPRT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]
